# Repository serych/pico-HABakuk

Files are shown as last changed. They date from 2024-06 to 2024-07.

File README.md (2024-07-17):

# Picoballoon tracker board based on RP2040
In this project I am developing a lightweight small balloon tracker board based on the RP2040 processor. 
The primary software intended for this board is [pico-WSPRer](https://github.com/EngineerGuy314/pico-WSPRer). 
## Basic parameters
- Board contains: 
    - RP2040 processor (with memory and crystal and RGB LED for status indication), 
    - position for soldering GPS module type ATGM336H (or pin compatible), 
    - SPV1040T MPPT inverter for solar cells 
- Flight interfaces: 
    - antenna, 
    - solar panels, 
    - ultracapacitor (optional), 
    - GPS antenna
    - additional GPIO pins GPIO10-GPIO13 + ADC0
- The pre-flight electronics parts are located on the breakaway part of the board, which is also equipped with test pins so that the flight part can be connected even after breakaway. 
- Pre-flight interfaces: 
    - USB connector and stabilizer for powering the board via USB, 
    - debug interface of RP2040, 
    - RESET and USB_BOOT buttons
## Images
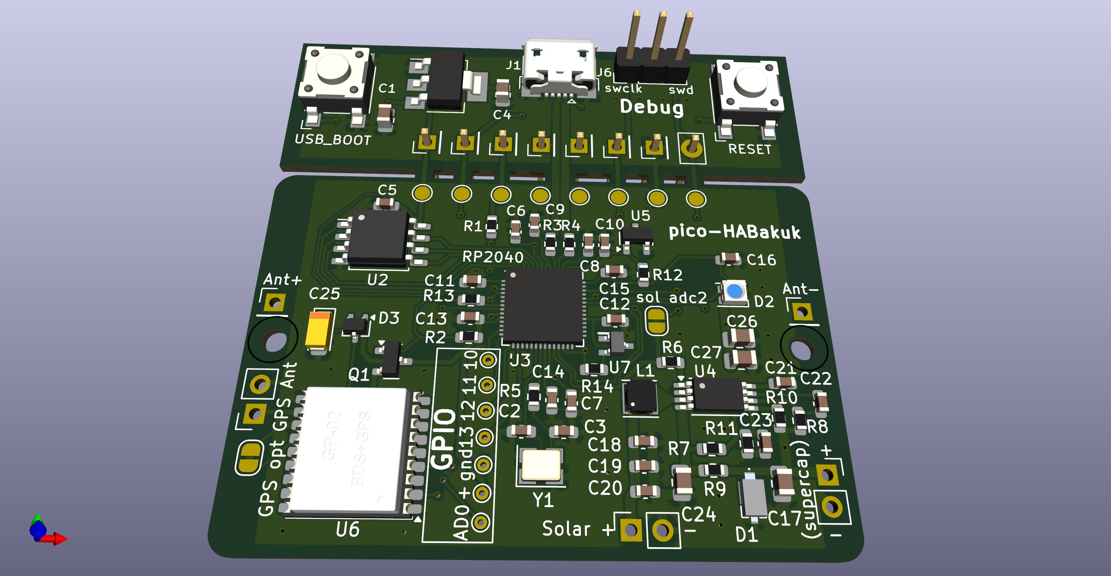
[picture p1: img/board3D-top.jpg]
3D model - top side

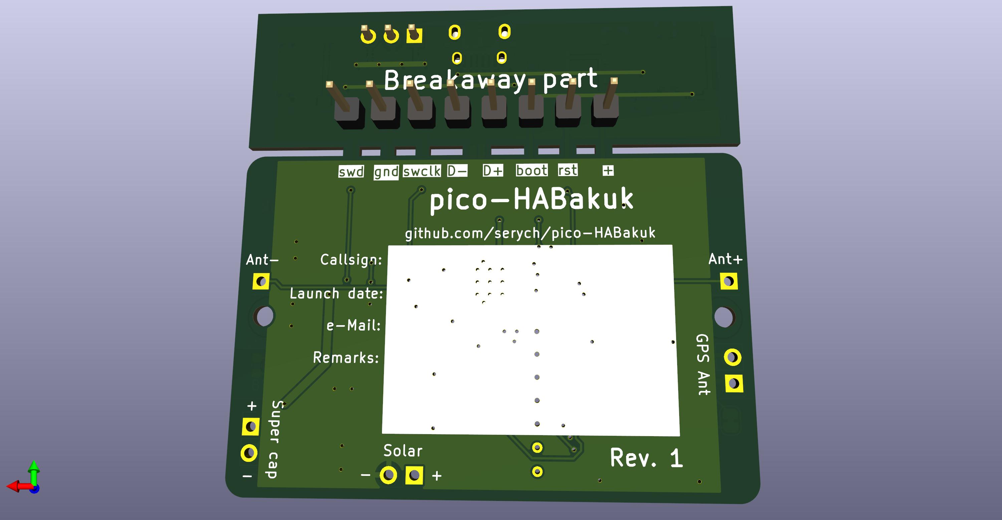
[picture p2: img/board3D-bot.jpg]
3D model - bottom side

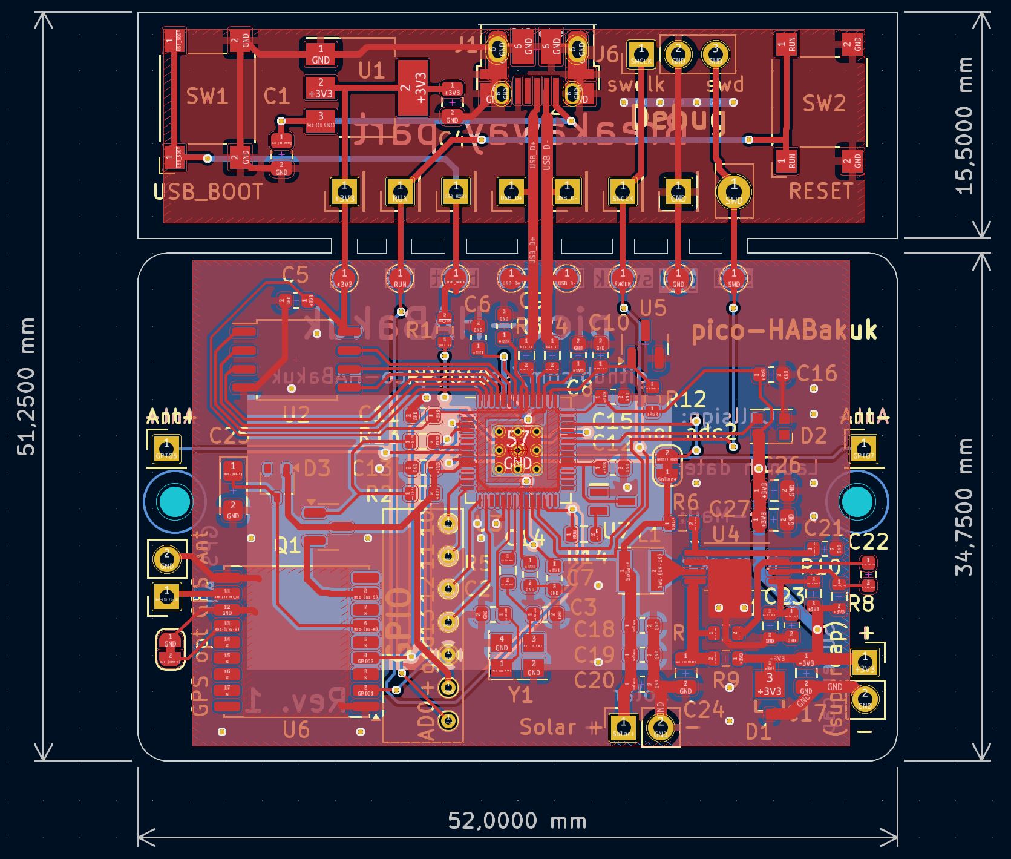
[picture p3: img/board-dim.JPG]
board dimensions


### This project is licensed under the terms of the CERN Open Hardware Licence Version 2 - Weakly Reciprocal.

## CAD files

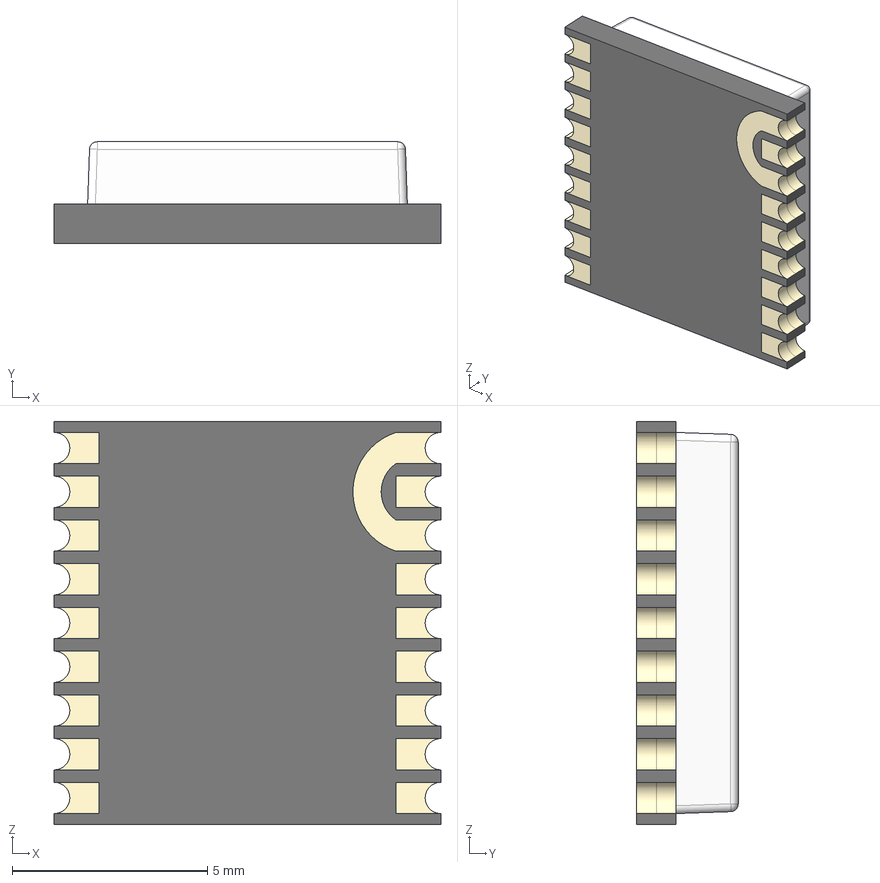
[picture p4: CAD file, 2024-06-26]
GP-02.stp
9.90 x 2.60 x 10.3 mm

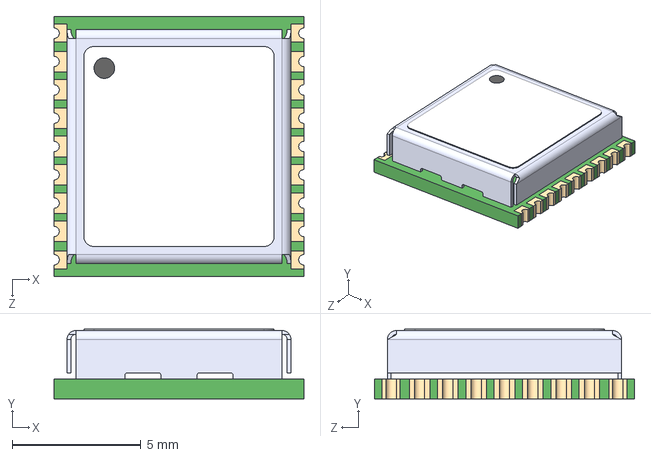
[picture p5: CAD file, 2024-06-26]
MAX-8Q-0.STEP
9.70 x 2.70 x 10.1 mm

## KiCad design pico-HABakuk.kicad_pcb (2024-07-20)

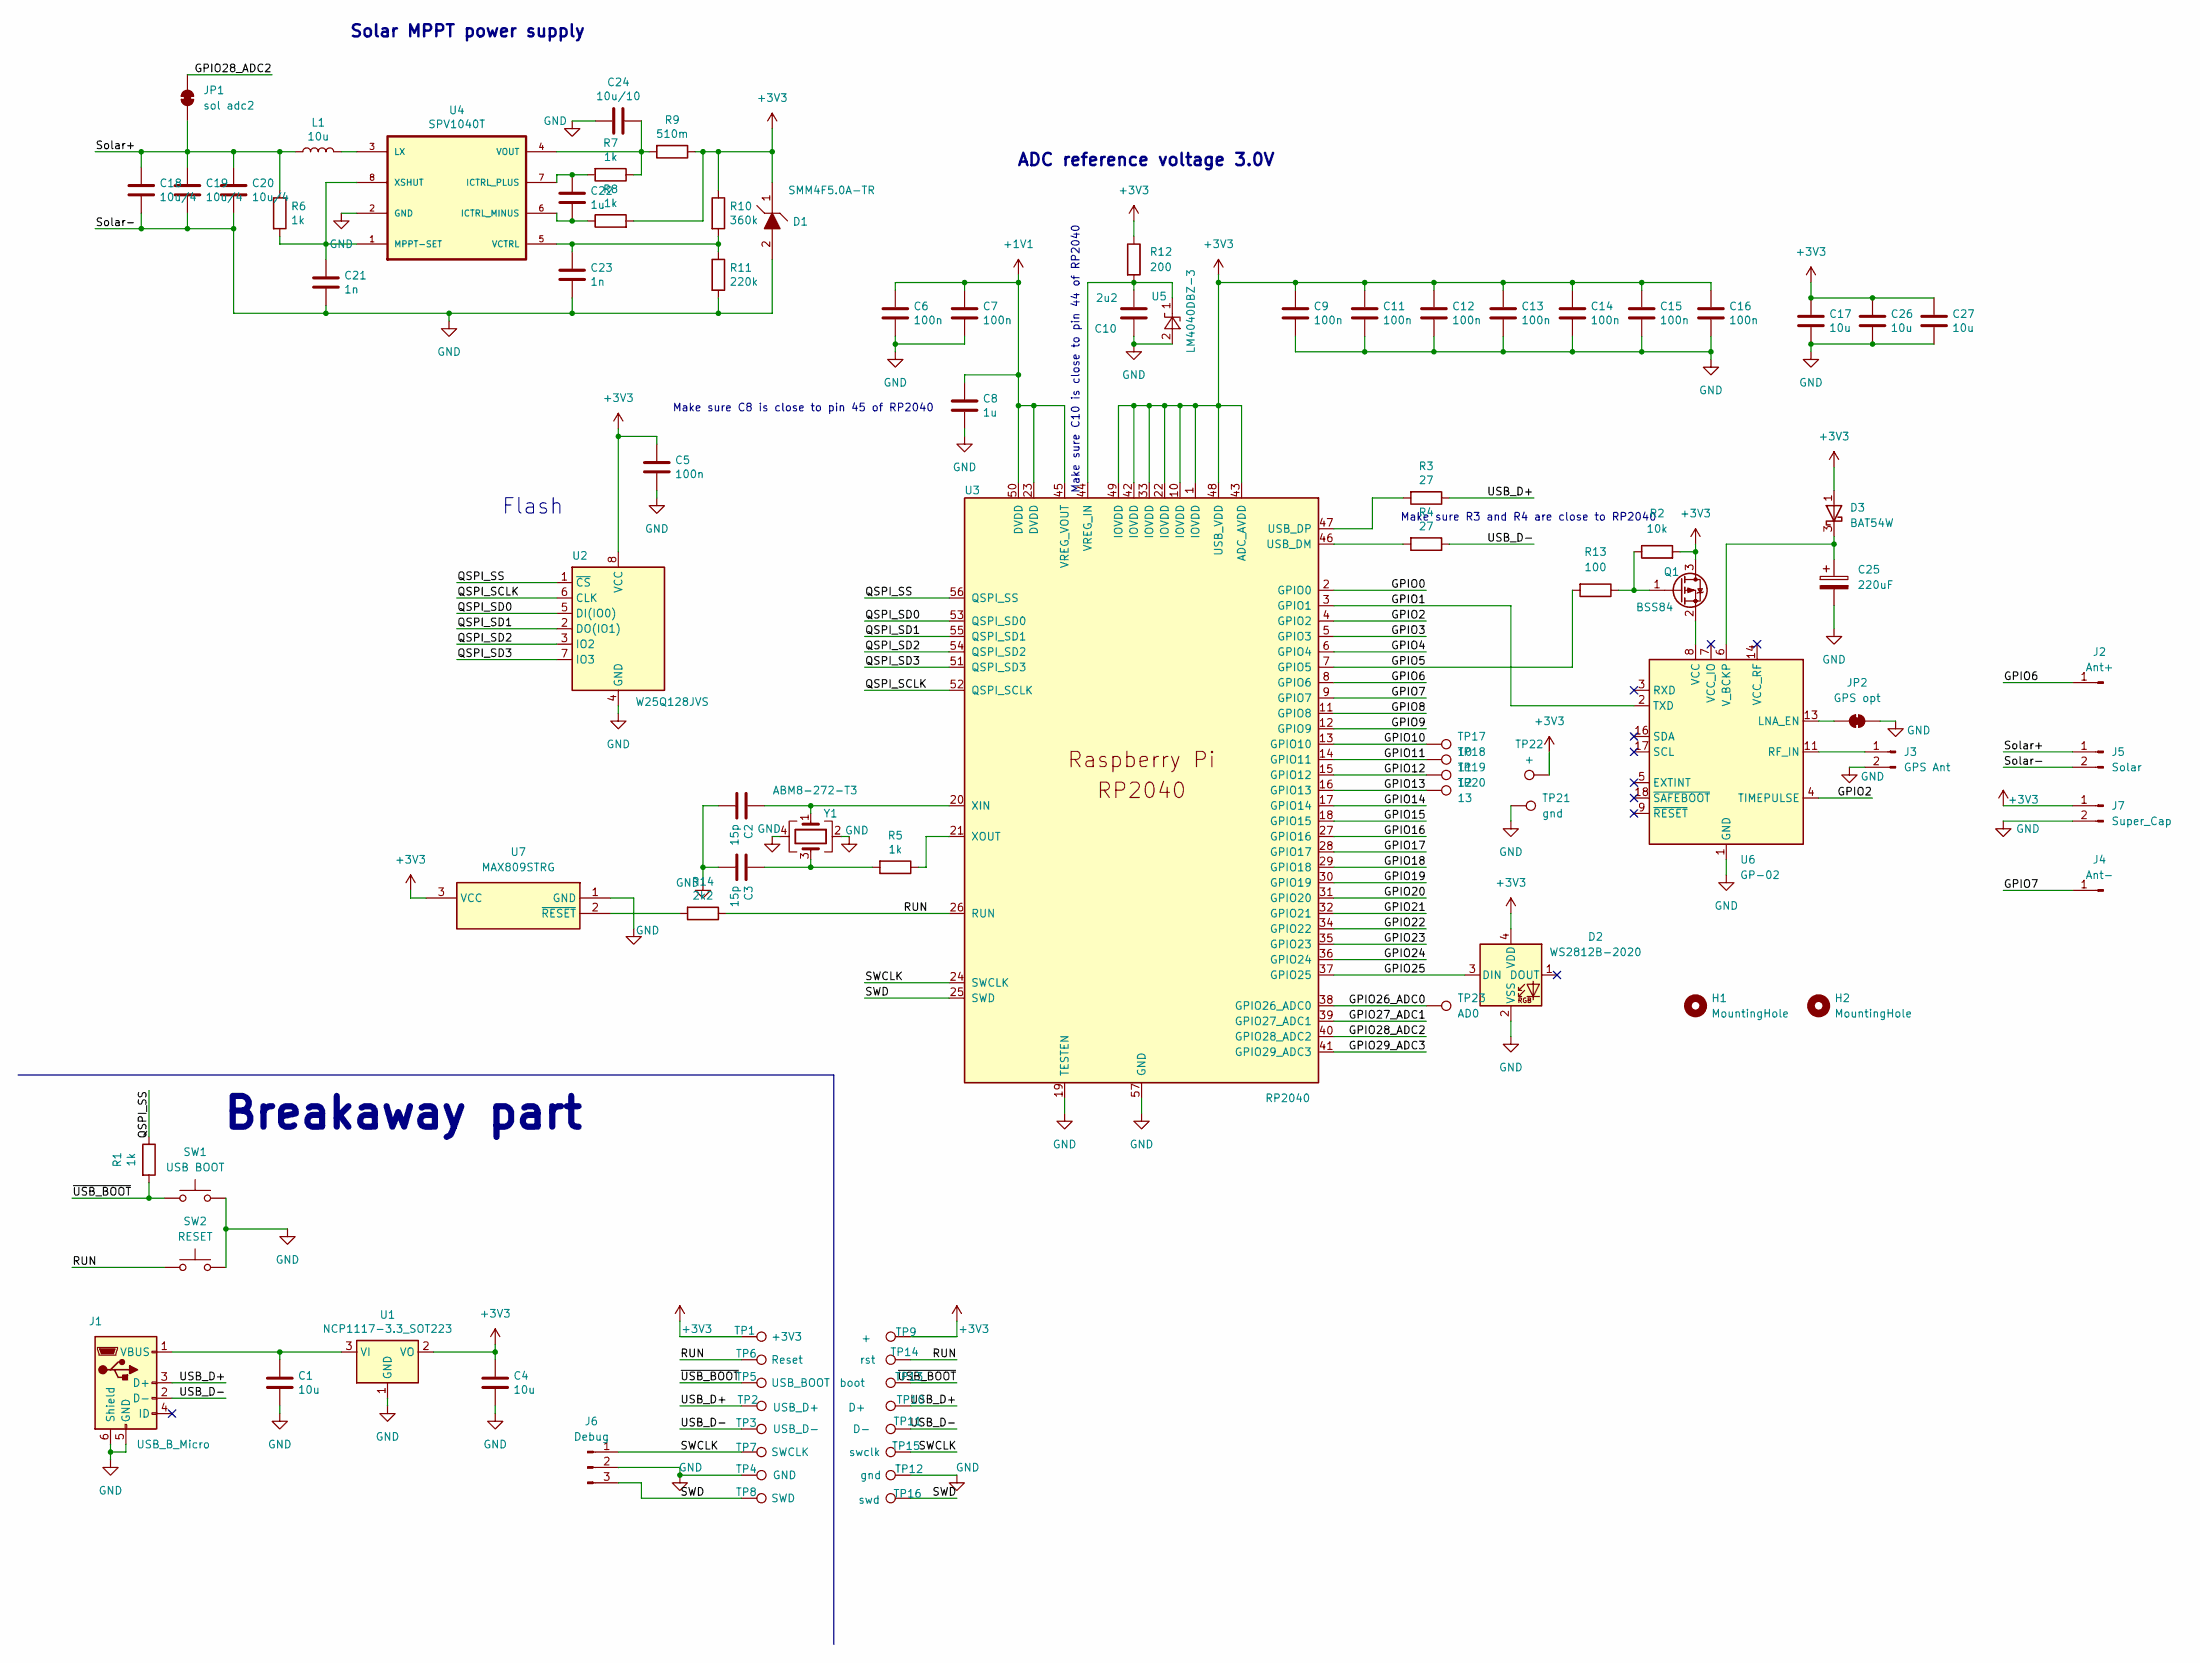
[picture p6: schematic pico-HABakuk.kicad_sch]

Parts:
C1, C4, C17, C26, C27: 10u; C_0805_2012Metric
C2, C3: 15p; C_0603_1608Metric
C5, C6, C7, C9, C11, C12, C13, C14, C15, C16: 100n; C_0603_1608Metric
C8, C22: 1u; C_0603_1608Metric
C10: 2u2; C_0603_1608Metric
C18, C19, C20: 10u/4; C_0603_1608Metric
C21, C23: 1n; C_0603_1608Metric
C24: 10u/10; C_0805_2012Metric
C25: 220uF; CP_EIA-3216-10_Kemet-I
D1: SMM4F5.0A-TR; SMM4F15ATR; Mouser Part Number 511-SMM4F5.0A-TR
D2: WS2812B-2020; LED_WS2812B-2020_PLCC4_2.0x2.0mm
D3: BAT54W; SOT-323_SC-70
H1, H2: MountingHole; MountingHole_2.1mm
J1: USB_B_Micro; USB_Micro-B_Amphenol_10103594-0001LF_Horizontal_modified
J2: Ant+; PinHeader_1x01_P2.54mm_Vertical
J3: GPS Ant; PinSocket_1x02_P2.54mm_Vertical
J4: Ant-; PinHeader_1x01_P2.54mm_Vertical
J5: Solar; PinSocket_1x02_P2.54mm_Vertical
J6: Debug; PinHeader_1x03_P2.54mm_Vertical
J7: Super_Cap; PinSocket_1x02_P2.54mm_Vertical
JP1: sol adc2; SolderJumper-2_P1.3mm_Bridged_RoundedPad1.0x1.5mm
JP2: GPS opt; SolderJumper-2_P1.3mm_Bridged_RoundedPad1.0x1.5mm
L1: 10u; L_Taiyo-Yuden_MD-3030
Q1: BSS84; SOT-23
R1, R5, R6, R7, R8: 1k; R_0603_1608Metric
R2: 10k; R_0603_1608Metric
R3, R4: 27; R_0603_1608Metric
R9: 510m; R_0603_1608Metric
R10: 360k; R_0603_1608Metric
R11: 220k; R_0603_1608Metric
R12: 200; R_0603_1608Metric
R13: 100; R_0603_1608Metric
R14: 2k2; R_0603_1608Metric
SW1: USB BOOT; SW_SPST_Omron_B3FS-100xP
SW2: RESET; SW_SPST_Omron_B3FS-100xP
TP1: +3V3; Pin_D1.1mm_L10.2mm_W3.5mm_Flat
TP2: USB_D+; Pin_D1.1mm_L10.2mm_W3.5mm_Flat
TP3: USB_D-; Pin_D1.1mm_L10.2mm_W3.5mm_Flat
TP4: GND; Pin_D1.1mm_L10.2mm_W3.5mm_Flat
TP5: USB_BOOT; Pin_D1.1mm_L10.2mm_W3.5mm_Flat
TP6: Reset; Pin_D1.1mm_L10.2mm_W3.5mm_Flat
TP7: SWCLK; Pin_D1.1mm_L10.2mm_W3.5mm_Flat
TP8: SWD; Pin_D1.1mm_L10.2mm_W3.5mm_Flat
TP9: +; TestPoint_Pad_D1.5mm
TP10: D+; TestPoint_Pad_D1.5mm
TP11: D-; TestPoint_Pad_D1.5mm
TP12: gnd; TestPoint_Pad_D1.5mm
TP13: boot; TestPoint_Pad_D1.5mm
TP14: rst; TestPoint_Pad_D1.5mm
TP15: swclk; TestPoint_Pad_D1.5mm
TP16: swd; TestPoint_Pad_D1.5mm
TP17: 10; TestPoint_THTPad_D1.0mm_Drill0.5mm
TP18: 11; TestPoint_THTPad_D1.0mm_Drill0.5mm
TP19: 12; TestPoint_THTPad_D1.0mm_Drill0.5mm
TP20: 13; TestPoint_THTPad_D1.0mm_Drill0.5mm
TP21: gnd; TestPoint_THTPad_D1.0mm_Drill0.5mm
TP22: +; TestPoint_THTPad_D1.0mm_Drill0.5mm
TP23: AD0; TestPoint_THTPad_D1.0mm_Drill0.5mm
U1: NCP1117-3.3_SOT223; SOT-223-3_TabPin2
U2: W25Q128JVS; SOIC-8_5.23x5.23mm_P1.27mm
U3: RP2040; RP2040-QFN-56
U4: SPV1040T; TSSOP-8_4.4x3mm_P0.65mm
U5: LM4040DBZ-3; SOT-23
U6: GP-02; ublox_MAX
U7: MAX809STRG; SOT65P210X110-3N; Mouser Part Number 700-MAX809SEXRT
Y1: ABM8-272-T3; Crystal_SMD_3225-4Pin_3.2x2.5mm

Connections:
+1V1: C6.1, C7.1, C8.1, U3.23 (DVDD), U3.45 (VREG_VOUT), U3.50 (DVDD)
+3V3: C4.1, C5.1, C9.1, C11.1, C12.1, C13.1, C14.1, C15.1, C16.1, C17.1, C26.1, C27.1, D1.1, D1.3, D2.4 (VDD), D3.1 (A), J7.1, Q1.3 (D), R2.2, R8.2, R9.1, R10.1, R12.1, TP1.1, TP9.1, TP22.1, U1.2 (VO), U2.8 (VCC), U3.1 (IOVDD), U3.10 (IOVDD), U3.22 (IOVDD), U3.33 (IOVDD), U3.42 (IOVDD), U3.43 (ADC_AVDD), U3.48 (USB_VDD), U3.49 (IOVDD), U7.3 (VCC)
/GPIO0: U3.2 (GPIO0)
/GPIO1: U3.3 (GPIO1), U6.2 (TXD)
/GPIO2: U3.4 (GPIO2), U6.4 (TIMEPULSE)
/GPIO3: U3.5 (GPIO3)
/GPIO4: U3.6 (GPIO4)
/GPIO5: R13.2, U3.7 (GPIO5)
/GPIO6: J2.1, U3.8 (GPIO6)
/GPIO7: J4.1, U3.9 (GPIO7)
/GPIO8: U3.11 (GPIO8)
/GPIO9: U3.12 (GPIO9)
/GPIO10: TP17.1, U3.13 (GPIO10)
/GPIO11: TP18.1, U3.14 (GPIO11)
/GPIO12: TP19.1, U3.15 (GPIO12)
/GPIO13: TP20.1, U3.16 (GPIO13)
/GPIO14: U3.17 (GPIO14)
/GPIO15: U3.18 (GPIO15)
/GPIO16: U3.27 (GPIO16)
/GPIO17: U3.28 (GPIO17)
/GPIO18: U3.29 (GPIO18)
/GPIO19: U3.30 (GPIO19)
/GPIO20: U3.31 (GPIO20)
/GPIO21: U3.32 (GPIO21)
/GPIO22: U3.34 (GPIO22)
/GPIO23: U3.35 (GPIO23)
/GPIO24: U3.36 (GPIO24)
/GPIO25: D2.3 (DIN), U3.37 (GPIO25)
/GPIO26_ADC0: TP23.1, U3.38 (GPIO26_ADC0)
/GPIO27_ADC1: U3.39 (GPIO27_ADC1)
/GPIO28_ADC2: JP1.2 (B), U3.40 (GPIO28_ADC2)
/GPIO29_ADC3: U3.41 (GPIO29_ADC3)
/QSPI_SCLK: U2.6 (CLK), U3.52 (QSPI_SCLK)
/QSPI_SD0: U2.5 (DI(IO0)), U3.53 (QSPI_SD0)
/QSPI_SD1: U2.2 (DO(IO1)), U3.55 (QSPI_SD1)
/QSPI_SD2: U2.3 (IO2), U3.54 (QSPI_SD2)
/QSPI_SD3: U2.7 (IO3), U3.51 (QSPI_SD3)
/QSPI_SS: R1.1, U2.1 (~CS), U3.56 (QSPI_SS)
/RUN: R14.1, SW2.1, TP6.1, TP14.1, U3.26 (RUN)
/SWCLK: J6.1, TP7.1, TP15.1, U3.24 (SWCLK)
/SWD: J6.3, TP8.1, TP16.1, U3.25 (SWD)
/Solar+: C18.1, C19.1, C20.1, J5.1, JP1.1 (A), L1.1, R6.1
/USB_D+: J1.3 (D+), R3.1, TP2.1, TP10.1
/USB_D-: J1.2 (D-), R4.1, TP3.1, TP11.1
/~USB_BOOT: R1.2, SW1.1, TP5.1, TP13.1
GND: C1.2, C2.2, C3.2, C4.2, C5.2, C6.2, C7.2, C8.2, C9.2, C10.2, C11.2, C12.2, C13.2, C14.2, C15.2, C16.2, C17.2, C18.2, C19.2, C20.2, C21.2, C23.2, C24.2, C25.2, C26.2, C27.2, D1.2, D2.2 (VSS), J1.5 (GND), J1.6 (Shield), J3.2, J5.2, J6.2, J7.2, JP2.1 (A), R11.2, SW1.2, SW2.2, TP4.1, TP12.1, TP21.1, U1.1 (GND), U2.4 (GND), U3.19 (TESTEN), U3.57 (GND), U4.2 (GND), U5.2 (A), U6.1 (GND), U6.10 (GND), U6.12 (GND), U7.1 (GND), Y1.2, Y1.4
unnamed: C3.1, R5.2, Y1.3
unnamed: C25.1, D3.3 (K), U6.6 (V_BCKP)
unnamed: C1.1, J1.1 (VBUS), U1.3 (VI)
unnamed: J3.1, U6.11 (RF_IN)
unnamed: JP2.2 (B), U6.13 (LNA_EN)
unnamed: Q1.1 (G), R2.1, R13.1
unnamed: Q1.2 (S), U6.8 (VCC)
unnamed: R4.2, U3.46 (USB_DM)
unnamed: R3.2, U3.47 (USB_DP)
unnamed: C10.1, R12.2, U3.44 (VREG_IN), U5.1 (K)
unnamed: C2.1, U3.20 (XIN), Y1.1
unnamed: R5.1, U3.21 (XOUT)
unnamed: C22.2, R8.1, U4.6 (ICTRL_MINUS)
unnamed: C22.1, R7.2, U4.7 (ICTRL_PLUS)
unnamed: L1.2, U4.3 (LX)
unnamed: C21.1, R6.2, U4.1 (MPPT-SET), U4.8 (XSHUT)
unnamed: C23.1, R10.2, R11.1, U4.5 (VCTRL)
unnamed: C24.1, R7.1, R9.2, U4.4 (VOUT)
unnamed: R14.2, U7.2 (~RESET)

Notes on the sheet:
ADC reference voltage 3.0V
Breakaway part
Make sure C8 is close to pin 45 of RP2040
Solar MPPT power supply
Make sure C10 is close to pin 44 of RP2040
Make sure R3 and R4 are close to RP2040
Flash

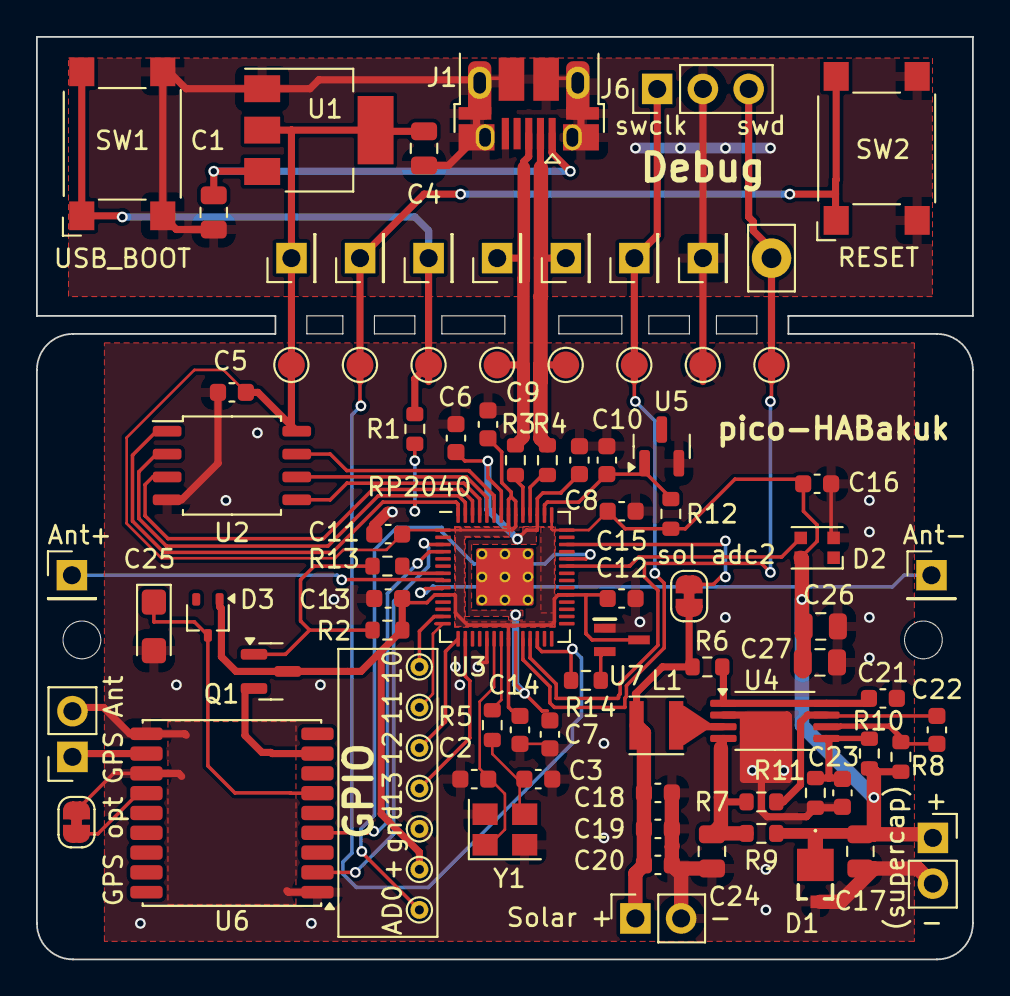
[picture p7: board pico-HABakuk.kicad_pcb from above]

Board: 2 copper layers, 52.0 x 51.2 mm, 90 parts (0 on the bottom side), 47 nets.

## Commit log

2024-06-15 Initial commit with RP2040 minimal board KiCAD project
    [pico-HABakuk.kicad_pcb, pico-HABakuk.kicad_sch]
2024-06-15 First changes in the sch and pcb
    [pico-HABakuk.kicad_pcb, pico-HABakuk.kicad_sch]
2024-06-16 Solar MPPT regulator copied into schema
    [pico-HABakuk.kicad_sch]
2024-06-16 adding parts to schematics
    [pico-HABakuk.kicad_sch]
2024-06-24 More work on schematics
    [pico-HABakuk.kicad_pcb, pico-HABakuk.kicad_sch]
2024-06-26 GPS module added to schematics
    [pico-HABakuk.kicad_pcb, pico-HABakuk.kicad_sch]
2024-06-26 GPS 3D model added
    [MAX-8Q-0.STEP, pico-HABakuk.kicad_pcb]
2024-06-26 another GPS module 3D model
    [GP-02.stp, pico-HABakuk.kicad_pcb]
2024-06-26 More work on schematics and PCB
    [pico-HABakuk.kicad_pcb, pico-HABakuk.kicad_sch]
2024-07-06 Max809 added
    [pico-HABakuk.kicad_pcb, pico-HABakuk.kicad_sch]
2024-07-10 Work on PCB
    [pico-HABakuk.kicad_pcb, pico-HABakuk.kicad_sch]
2024-07-17 board finetuning, GPIO pins added
    [pico-HABakuk.kicad_pcb, pico-HABakuk.kicad_sch]
2024-07-20 Final board tuning and DRC debuging
    [pico-HABakuk.kicad_pcb, pico-HABakuk.kicad_sch]
2024-07-20 HTML BOM added
2024-07-20 Minor silkscreen edits
    [pico-HABakuk.kicad_pcb, pico-HABakuk.kicad_sch]
2024-07-20 Gerber files generated
    [pico-HABakuk-B_Cu.gbr, pico-HABakuk-B_Mask.gbr, pico-HABakuk-B_Paste.gbr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]
2024-07-20 Gerber ziped
